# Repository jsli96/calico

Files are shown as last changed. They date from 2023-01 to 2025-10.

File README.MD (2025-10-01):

# Calico 🤖

Teaser

**Calico** is a miniature relocatable wearable system with fast and precise locomotion for on-body interaction, actuation and sensing. 
Calico consists of a two-wheel robot and an on-cloth track mechanism or "railway," on which the robot travels. 
The robot is self-contained, small in size, and has additional sensor expansion options. 
The Calico robot can adapt for various applications and target for different audience such as older adults, dancers, and children. 
For example, we designed **[Dance^2](https://dancesquared.xyz/)** with Calico to explore new forms of dance and movement, and to create a new form of interaction.
We also investigate how **[Calico for older adults](https://dl.acm.org/doi/10.5555/3721488.3721562)** can assist with daily activities and provide companionship. 

Please see the [Calico website](https://smartlab.cs.umd.edu/publication/calico) and [papers](https://dl.acm.org/doi/10.1145/3715336.3735828) for more details on the design and applications of Calico, and if you use Calico in your work, please consider to cite the following papers:
```
@article{sathya2022calico,
  title={Calico: Relocatable On-cloth Wearables with Fast, Reliable, and Precise Locomotion},
  author={Sathya, Anup and Li, Jiasheng and Rahman, Tauhidur and Gao, Ge and Peng, Huaishu},
  journal={Proceedings of the ACM on Interactive, Mobile, Wearable and Ubiquitous Technologies},
  volume={6},
  number={3},
  pages={1--32},
  year={2022},
  publisher={ACM New York, NY, USA}
}
```

```
@inproceedings{sathya2025cybernetic,
  title={Cybernetic Marionette: Channeling Collective Agency Through a Wearable Robot in a Live Dancer-Robot Duet},
  author={Sathya, Anup and Li, Jiasheng and Yan, Zeyu and Fang, Adriane and Kules, Bill and Martin, Jonathan David and Peng, Huaishu},
  booktitle={Proceedings of the 2025 ACM Designing Interactive Systems Conference},
  pages={3326--3340},
  year={2025}
}
```
```
@inproceedings{antony2025design,
  title={The design of on-body robots for older adults},
  author={Antony, Victor Nikhil and Jeon, Clara and Li, Jiasheng and Gao, Ge and Peng, Huaishu and Ostrowski, Anastasia K and Huang, Chien-Ming},
  booktitle={2025 20th ACM/IEEE International Conference on Human-Robot Interaction (HRI)},
  pages={589--598},
  year={2025},
  organization={IEEE}
}
```

---

## 📦 Table of Contents

- [Features](#-features)  
- [Hardware setup (BOM)](#-hardware)  
- [Arduino configuration](#arduino-configuration)
- [Connect & control the robot](#connect--control-the-robot)
- [Tips](#tips)

---

## ✨ Features

- MCU: ESP32 S3-Zero (Powered by [Waveshare](https://www.waveshare.com/wiki/ESP32-S3-Zero)) 
- Graphical user interface (GUI) for real time control
- Wi-Fi connection and controlled
- LED strip for visual feedback
- DC Motor Driver: DRV 8835
- LiPo's battery powered and charge via USB-C

---

## 🔧 Hardware

### Robot body and tracks 
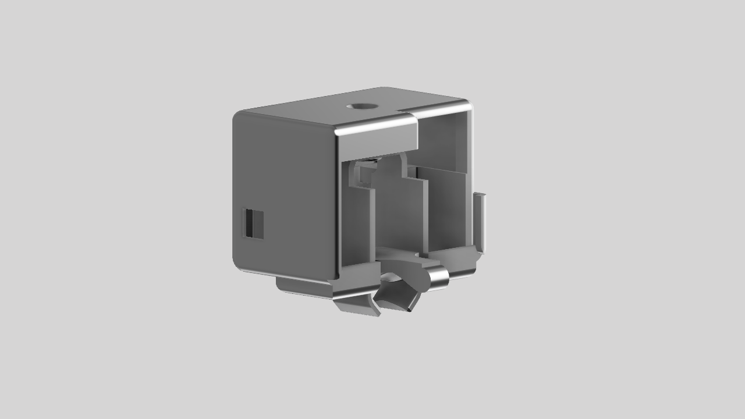
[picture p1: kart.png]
Robot body

- [Main body](./3D%20print%20models) 
  - 3D print material: PLA or Carbon PLA
  - Recommended print settings: 
    - Layer height: 0.2mm
    - Infill: 20% (or more for stronger body)
    - Print angle: 30 degrees
    - Supports: Yes 
  - Bamboo project file is included for reference: [3MF file](./3D%20print%20models/main_body.3mf)

- [Body cap](./3D%20print%20models) (Recommended setting same as above)
  - Require M2 screws and insert nuts to attach the body cap to the main body.
- [Wheels](./3D%20print%20models) (3D print material: PLA or Carbon PLA)
- [Track](./3D%20print%20models)
  - 3D print material: TPU Shore-95A
  - Recommended print settings: 
    - Layer height: 0.2mm
    - Infill: 20% 
    - Print angle: Flat (0 degrees)
    - Supports: Yes 
  - Bamboo project file is included for reference: [3MF file](./3D%20print%20models/track.3mf)
  - Tracks are designed in modular pieces, and you can print multiple pieces to create a longer track. 
    To connect the track pieces, you need a 1.75mm filament (e.g., PLA) and insert them into designed holes at the both end of the track pieces.
    
  - See below figures for references.
    Track assembly

### Robot electronics
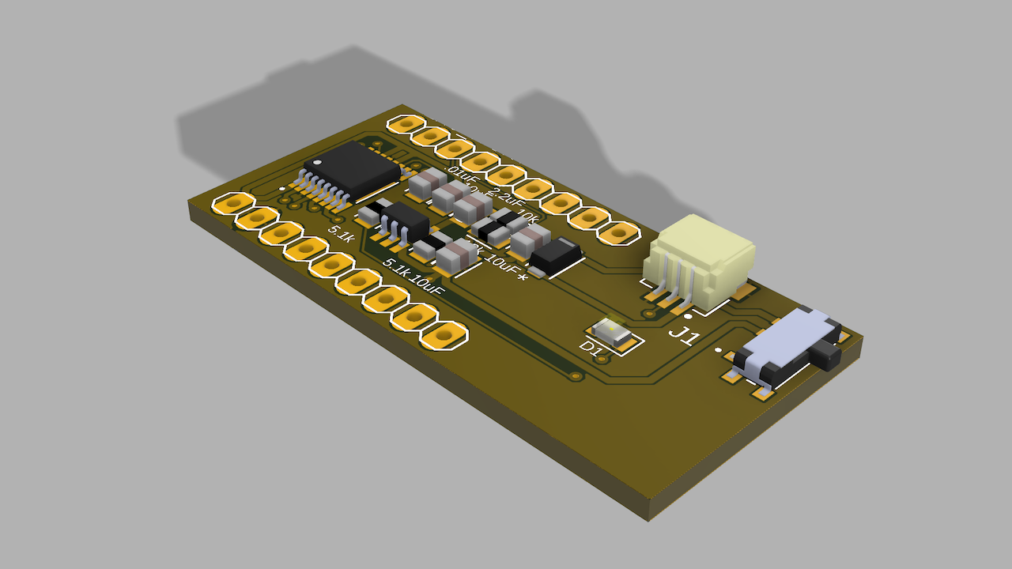
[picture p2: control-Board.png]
PCB

- MCU ([ESP32 S3-Zero](https://www.waveshare.com/wiki/ESP32-S3-Zero))
- Custom PCB ([See PCB folder for details](./PCB%20files))
- N20 DC motors
- LED strip (4 LEDs)
- 3.7V LiPo battery

---

## Arduino Configuration
The robot is powered by an ESP32 S3-Zero, which is programmed using the Arduino IDE. 
Please refer to the below steps to set up the Arduino IDE for Calico.
- Install the [Arduino IDE](https://www.arduino.cc/en/software).
- Open Arduino IDE settings (Mac Version) `Arduino IDE` (the top-left corner on the screen) > `Settings`, (Win version) `File` > `Preferences` 
- Adding the following URL to the "Additional Boards Manager URLs" field:
  ```
  https://dl.espressif.com/dl/package_esp32_index.json
  ```
- Open the Boards Manager from `Tools` > `Board` > `Boards Manager`, search for `esp32`. Then install the latest version of `esp32 by Espressif Systems`.
- Select the ESP32 S3-Zero board from `Tools` > `Board` > `ESP32 S3 Dev Module`.
- Refer to the below image to configure the ESP32 settings:
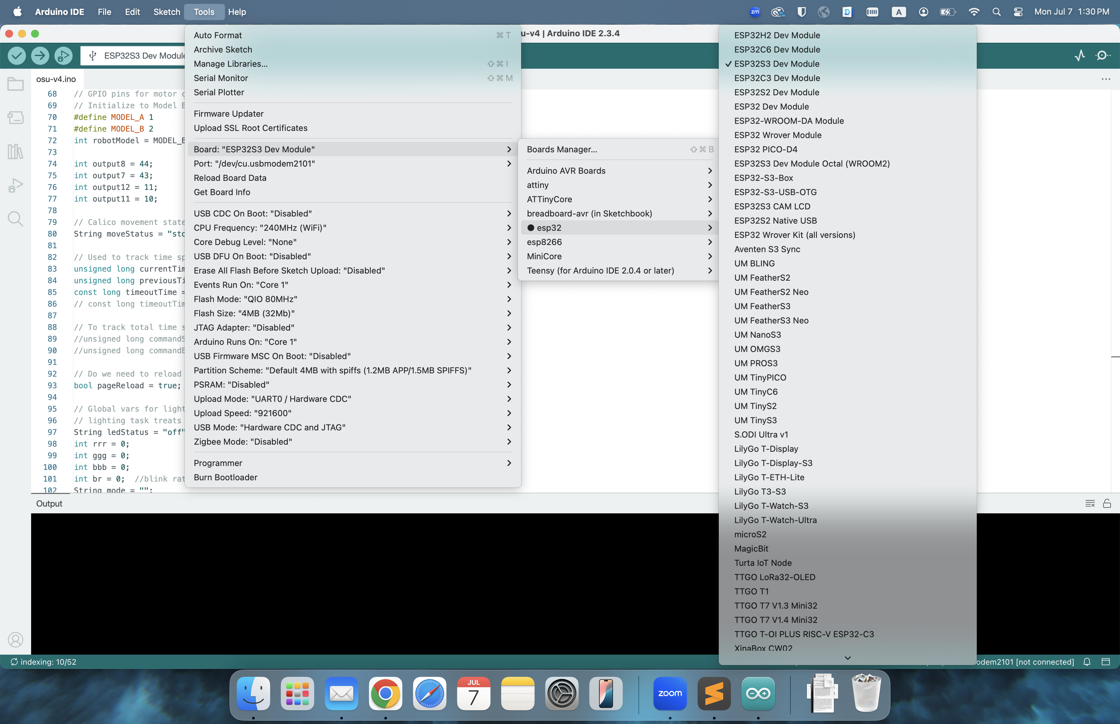
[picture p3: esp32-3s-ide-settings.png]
ESP32-S3
- 

---

## Connect & control the robot
To connect and control the robot, follow these steps:
1. **Connect the robot to your computer** using a USB-C cable.
2. **Open the Arduino IDE** and select the correct port from `Tools` > `Port`.
3. **Change the WiFi credentials** in the `main_app.ino' file (line 46 - 49) to match your network:
   ```
   const char* ssid_dev = "your-ssid";
   const char* password_dev = "your-password";
   const char* ssid = "your-ssid";
   const char* password = "your-password";
   ```
4. **Upload the code** to the ESP32 S3-Zero by clicking the upload button in the Arduino IDE. (You only need to do this once. 
After you have updated the Wi-Fi credentials and uploaded the code into Calico robot, you can control the robot without needing to upload the code again.)
   - Make sure you have the correct board and port selected in the Arduino IDE.
   - The upload process may take a few minutes, and you will see the progress in the console at the bottom of the IDE.
5. Once the upload is complete, open the Serial Monitor from `Tools` > `Serial Monitor` to see the connection status.
6. If the robot connects successfully, you will see a message indicating the IP address assigned to the robot.
7. **Open the GUI** by navigating to the IP address in your web browser. The GUI will allow you to control the robot's movement and LED strip.

## Tips
1. The robot will light up the LED light on board in different colors based on its status:
   - **light off**: Robot not powered
   - **steady blue**: Wi-Fi connected
   - **flashing blue**: Trying to connect Wi-Fi
   
2. If you can not see the ip address from the serial port you can use LanScan tools to find the IP address of the robot. 
   - For example, you can use [LanScan](https://apps.apple.com/us/app/lanscan/id472226235?mt=12) or [Advanced IP Scanner](https://www.advanced-ip-scanner.com/).

3. Battery connector is JST PH 2.0, and motor and LED connectors are JST SH 1.0.
4. The robot can be charged via USB-C port. (**be careful with the battery +/- directions**)
   - The battery is 3.7V LiPo battery, and the charging current is 500mA.
   - The battery can be replaced if needed.

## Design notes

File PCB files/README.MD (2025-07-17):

This is the PCB files folder for the Calico project. It contains the schematic and PCB design files for the custom control board used in the Calico robot.
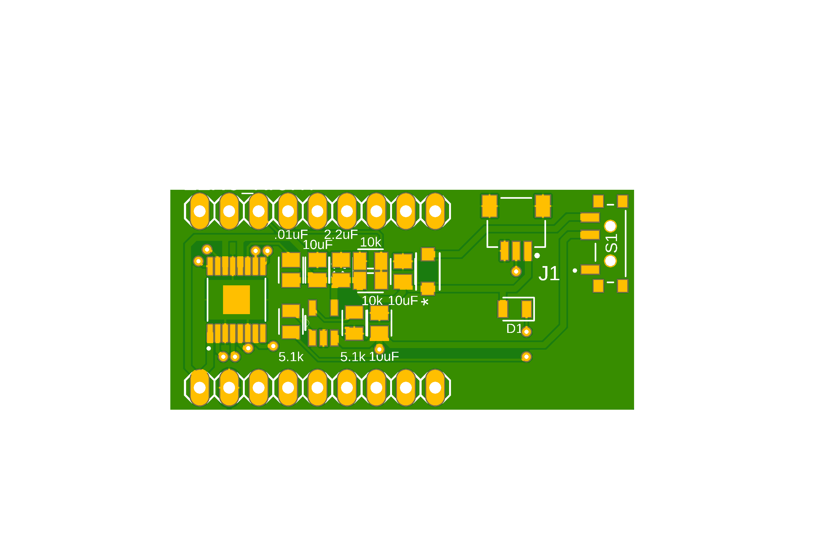
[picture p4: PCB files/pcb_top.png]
PCB-TOP

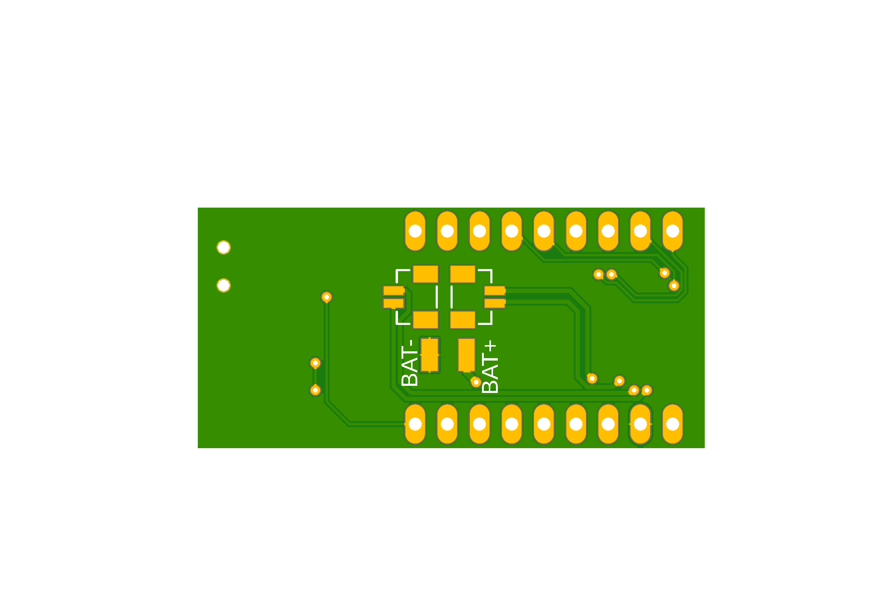
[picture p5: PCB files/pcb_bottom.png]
PCB-Bottom


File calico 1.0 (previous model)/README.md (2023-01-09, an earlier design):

# calico
Calico project

This project originally created and implemented by Anup (https://github.com/anupsathya/calico). 

This is a simplify version to help future development.

Change log:

Motor driver: DRV8833
```
  Motor 1: D25
           D22
  Motor 2: D19
           D17
```
RGB LED port: ```D5```

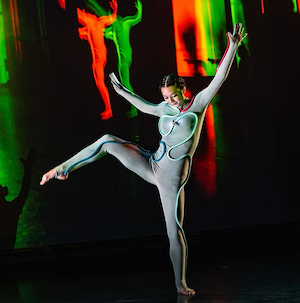
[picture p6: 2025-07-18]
calico_dancers.png

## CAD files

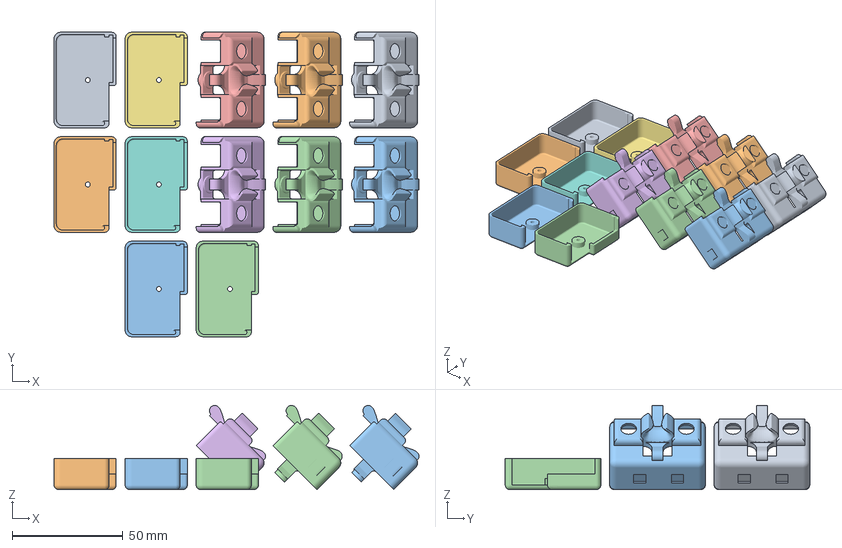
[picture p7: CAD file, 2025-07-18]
3D print models/main_body.3mf
164.5 x 137.3 x 37.9 mm
Main body.stl x 6
Body19.stl x 6

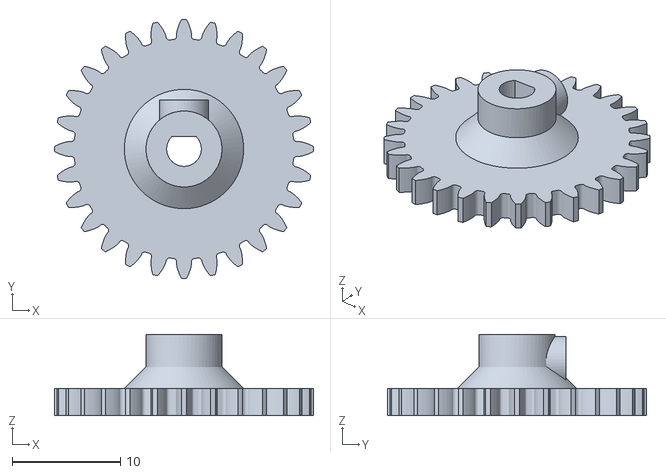
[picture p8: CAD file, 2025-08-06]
3D print models/wheel.stl
23.9 x 23.9 x 7.50

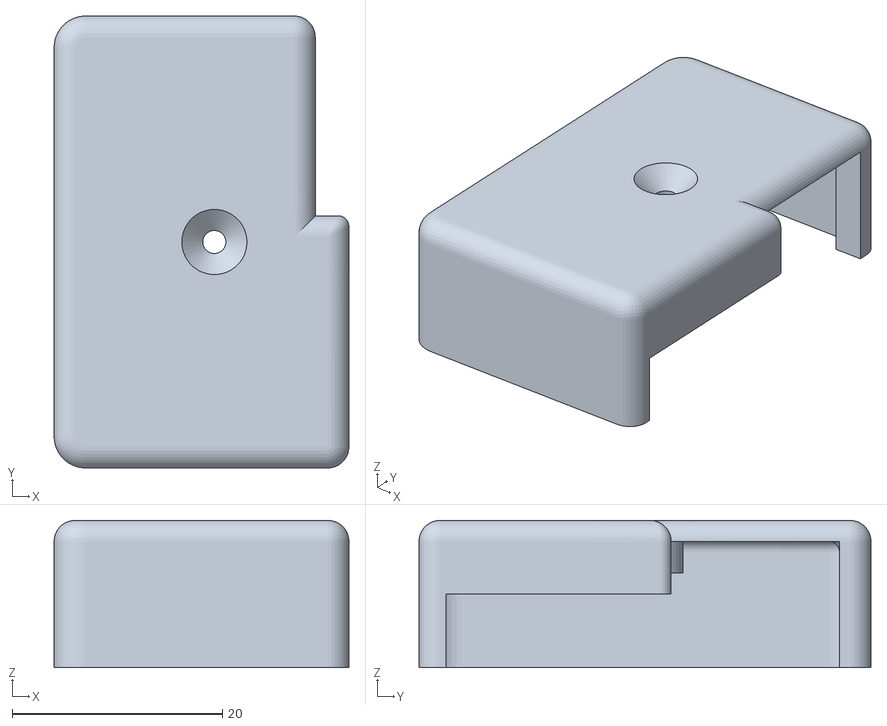
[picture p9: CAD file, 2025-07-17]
3D print models/cap.stl
28.1 x 43.0 x 14.0

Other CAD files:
3D print models/main_body.stl

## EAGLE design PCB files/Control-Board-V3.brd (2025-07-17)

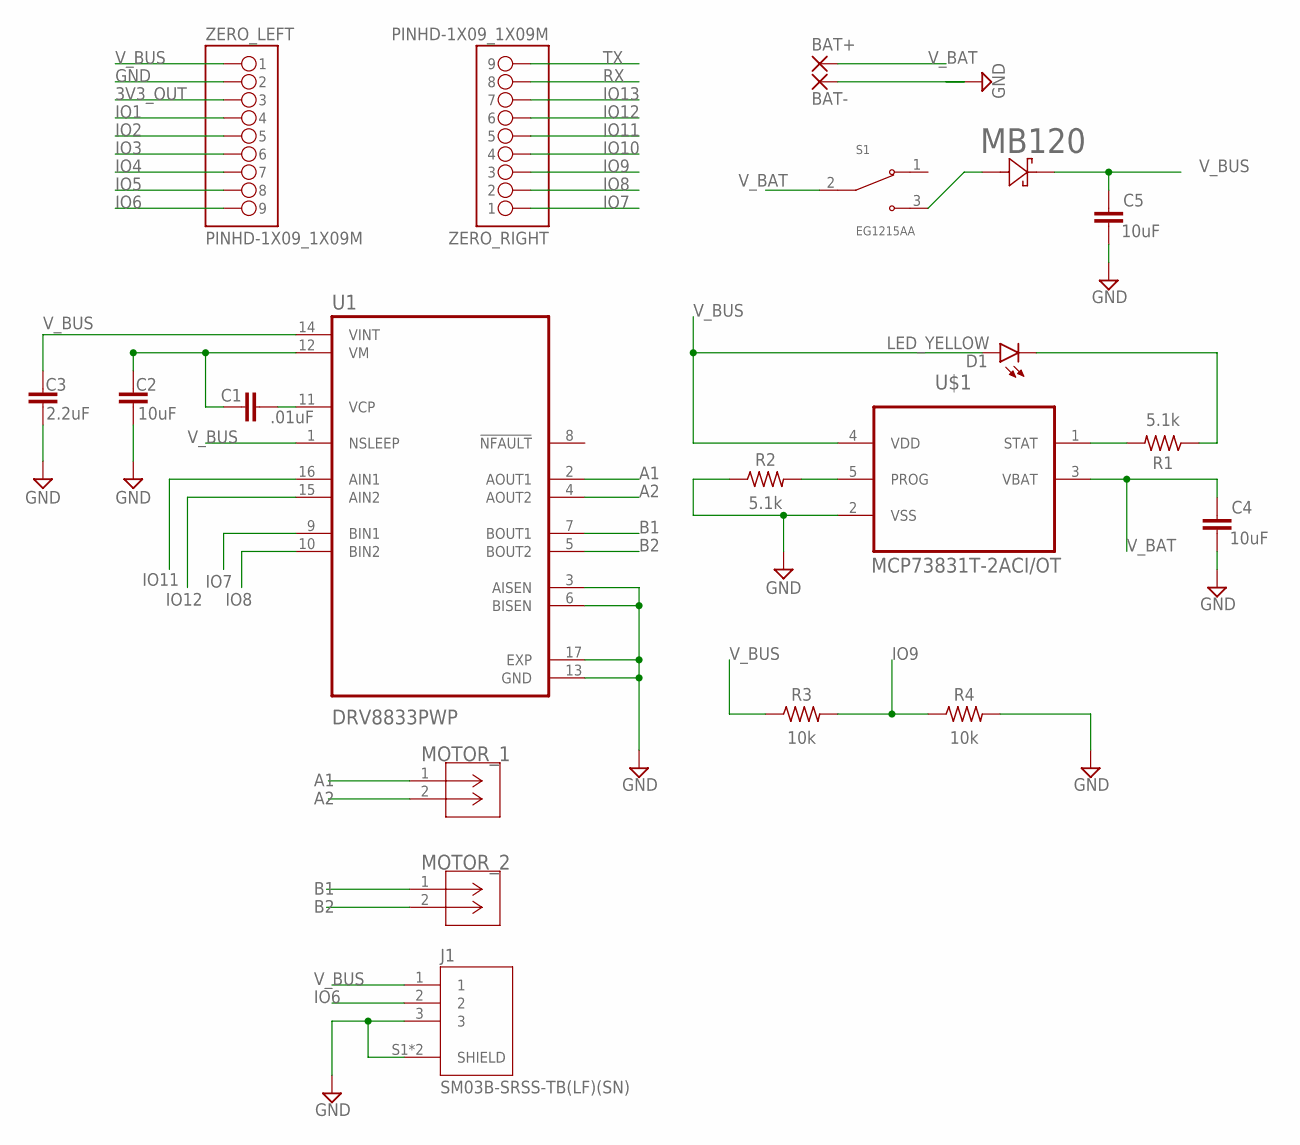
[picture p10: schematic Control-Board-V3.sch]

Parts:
BAT+: SMD2; SMD1,27-2,54
BAT-: SMD2; SMD1,27-2,54
C1: .01uF; CAPC2012X110
C2, C4, C5: 10uF; CAPC2012X110
C3: 2.2uF; CAPC2012X110
D1: LED_YELLOW; LEDC2012X110N_FLAT-Y
J1: SM03B-SRSS-TB(LF)(SN); JST_SM03B-SRSS-TB(LF)(SN)
MB120: MBR120LSFT3GSDO_SOD-123FL(498)_OSI-L; SDO_SOD-123FL(498)_OSI-L
MOTOR_1, MOTOR_2: JST_SH; JST
R1, R2: 5.1k; RESC2012X65
R3, R4: 10k; RESC2012X65
S1: EG1215AA; SW_EG1215AA
U1: DRV8833PWP; IC_DRV8833PWP
U$1: MCP73831T-2ACI/OT; SOT95P280X145-5N
ZERO_LEFT: PINHD-1X09_1X09M; 1X09
ZERO_RIGHT: PINHD-1X09_1X09M; 1X09

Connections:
3V3_OUT: ZERO_LEFT.3
A1: MOTOR_1.1, U1.2 (AOUT1)
A2: MOTOR_1.2, U1.4 (AOUT2)
B1: MOTOR_2.1, U1.7 (BOUT1)
B2: MOTOR_2.2, U1.5 (BOUT2)
GND: BAT-.1, C2.1, C3.1, C4.2, C5.2, J1.3, J1.S1 (SHIELD), J1.S2 (SHIELD), R2.1, R4.2, U1.3 (AISEN), U1.6 (BISEN), U1.13 (GND), U1.17 (EXP), U$1.2 (VSS), ZERO_LEFT.2
IO1: ZERO_LEFT.4
IO2: ZERO_LEFT.5
IO3: ZERO_LEFT.6
IO4: ZERO_LEFT.7
IO5: ZERO_LEFT.8
IO6: J1.2, ZERO_LEFT.9
IO7: U1.9 (BIN1), ZERO_RIGHT.1
IO8: U1.10 (BIN2), ZERO_RIGHT.2
IO9: R3.2, R4.1, ZERO_RIGHT.3
IO10: ZERO_RIGHT.4
IO11: U1.16 (AIN1), ZERO_RIGHT.5
IO12: U1.15 (AIN2), ZERO_RIGHT.6
IO13: ZERO_RIGHT.7
unnamed: C1.2, U1.11 (VCP)
unnamed: R1.2, U$1.1 (STAT)
unnamed: D1.C, R1.1
unnamed: R2.2, U$1.5 (PROG)
unnamed: MB120.2, S1.3
RX: ZERO_RIGHT.8
TX: ZERO_RIGHT.9
V_BAT: BAT+.1, C4.1, S1.2, U$1.3 (VBAT)
V_BUS: C1.1, C2.2, C3.2, C5.1, D1.A, J1.1, MB120.1, R3.1, U1.1 (NSLEEP), U1.12 (VM), U1.14 (VINT), U$1.4 (VDD), ZERO_LEFT.1

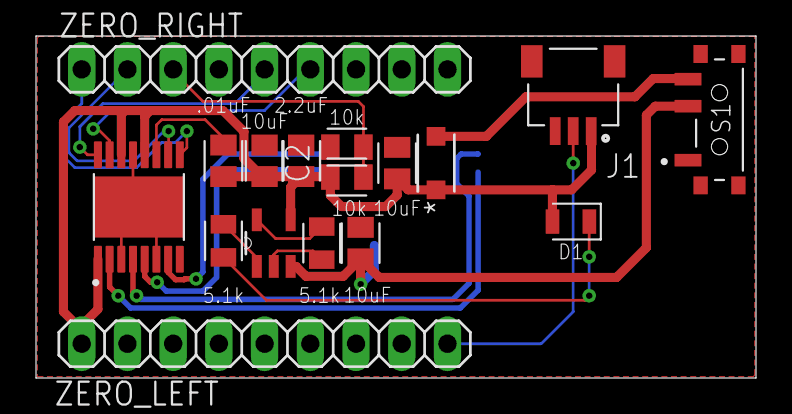
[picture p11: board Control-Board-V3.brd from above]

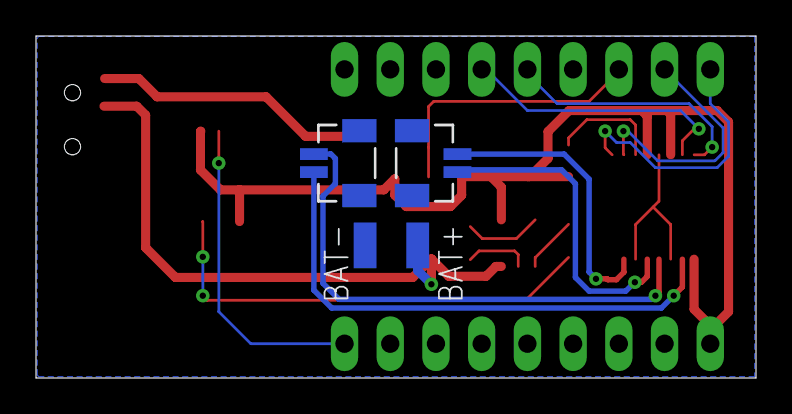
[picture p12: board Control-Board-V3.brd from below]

Board: 2 copper layers, 40.0 x 19.0 mm, 21 parts (4 on the bottom side), 18 nets.

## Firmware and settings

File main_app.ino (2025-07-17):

#include <WiFi.h>
#include <WiFiAP.h>
#include <WiFiClient.h>
#include <WiFiGeneric.h>
#include <WiFiMulti.h>
#include <WiFiSTA.h>
#include <WiFiScan.h>
#include <WiFiServer.h>
#include <WiFiType.h>
#include <WiFiUdp.h>

/*********
  Calico web control
  
  osc-v3 - 
  
  4/10 originally cloned from ..._ff_v02
  4/10 - change slow bink to go a bit quicker and fast blink to go a little slower
  4/12 - remove fade up/down; implement white light, multicolor and ALL OFF; reworked UI; tweaked slow blink duration 
  4/17 - added pulsate modes; bigger buttons; minor UI cleanups; removed unused mode colorsequence
  5/11 - add 2 vibrate modes
  5/13 - add nightlight mode
  12/12 - started OSU version - combined calico_sp24wk_1 with GPIO pin changes
  12/14 - streamlined serial printing; reduced timeoutTime to improve responsiveness
  12/20 - tweak code to show onboard & NeoPixel lights closer to the same time; pin lighting task to core 0; 
          streamline HTML printing
  1/7/2025 - Use XMLHttpRequest - Only reload page if empty request; otherwise just report result; trimmed HTML to 
          remove <a> and just leave <button>s. Anyone can send this request - QLab, Isadora, webdb server, etc. -
          as long as they have the right IP address.
  1/8/2025 - Add code to handle two robot models, which have different motor control pin assignments:
             Model A - original board, non-charging
             Model B - current board
  1/13/2025 - Keep LEDs dim after initial prod network connection AND when trying to connect to dev network

  To Do:
  - Set color w fade duration - keep current color
  
  Bugs:
  - if we get too many requests at once it drops things

  ********/

const char* calico_version = "mian_app";  // Make sure this matches file name

// Network credentials
const char* ssid_dev = "TP-LINK_lab0102";
const char* password_dev = "LAB0102!!!";
const char* ssid = "WIFI_0102";
const char* password = "admin0102";

#include <WiFi.h>
#include <Adafruit_NeoPixel.h>

// Pixel setup
#define LEDS_COUNT 4
#define LEDS_PIN 6
Adafruit_NeoPixel on_board_led(1, 21, NEO_RGB);
Adafruit_NeoPixel strip_led(LEDS_COUNT, LEDS_PIN, NEO_GRB);  // Note R/G are reversed compared to onboard LED

// Web server setup
WiFiServer server(80);
WiFiClient client;
String header;  // HTTP request
String ipAddr;

// Calico setup

// GPIO pins for motor control - we now support two robot models - see below
// Initialize to Model B - current
#define MODEL_A 1
#define MODEL_B 2
int robotModel = MODEL_B;

int output8 = 44;
int output7 = 43;
int output12 = 11;
int output11 = 10; 

// Calico movement state variable
String moveStatus = "stop";

// Used to track time spent reading client request - to make sure we don't hang indefinitely
unsigned long currentTime = millis();
unsigned long previousTime = 0;
const long timeoutTime = 200;  // Millisecs
// const long timeoutTime = 5000;  // Millisecs 

// To track total time spent processing each request
//unsigned long commandStart = 0;
//unsigned long commandEnd = 0;

// Do we need to reload entire page?
bool pageReload = true; // initially yes

// Global vars for lighting task
// lighting task treats these as read-only to avoid race conditions
String ledStatus = "off";
int rrr = 0;
int ggg = 0;
int bbb = 0;
int br = 0;  //blink rate in msecs (really this is the duration of half a cycle)
String mode = "";


// setColor - set color of onboard and LED strip
void setColor(uint32_t c) {
  on_board_led.setPixelColor(0, c);
  strip_led.fill(c);
  on_board_led.show();
  strip_led.show();
}

// In the future: Convert this to a fade up and down of blue... and call it from the lightign task... and create a button
// fadeColorOff - fade off over duration of time
// Use of vTaskDelay won't necessarily provide a consistent frequency - can use vTaskDelayUntil if needed
void fadeColorUp(int dur) {
  // char s[80];
  // sprintf(s, "fadeColorUp(): dur=%d\n", dur);
  // Serial.println (s);

  int iters = dur / 50;
  if (iters < 1) iters = 1;
  int inc_r = rrr / iters;
  int inc_g = ggg / iters;
  int inc_b = bbb / iters;
  int cur_r = 0;
  int cur_g = 0;
  int cur_b = 0;
  for (int i = 0; i < iters; i++) {
    cur_r += inc_r;
    cur_g += inc_g;
    cur_b += inc_b;
    setColor(Adafruit_NeoPixel::Color(cur_r, cur_g, cur_b));
    vTaskDelay(50 / portTICK_PERIOD_MS);  // converts msecs to ticks
  }
}

void fadeColorDown(int dur) {
  // char s[80];
  // sprintf(s, "fadeColorDown(): dur=%d\n", dur);
  // Serial.println (s);

  int iters = dur / 50;
  if (iters < 1) iters = 1;
  int inc_r = rrr / iters;
  int inc_g = ggg / iters;
  int inc_b = bbb / iters;
  int cur_r = rrr;
  int cur_g = ggg;
  int cur_b = bbb;
  for (int i = 0; i < iters; i++) {
    cur_r -= inc_r;
    cur_g -= inc_g;
    cur_b -= inc_b;
    setColor(Adafruit_NeoPixel::Color(cur_r, cur_g, cur_b));
    vTaskDelay(50 / portTICK_PERIOD_MS);  // converts msecs to ticks
  }
}

// Lighting task setup
// Uses global var ledStatus as state variable
void lightingTask(void* parameters) {
  int count = 0;
  Serial.print("Lighting task running on core ");
  Serial.println(xPortGetCoreID());
  for (;;) {
    //  Serial.println("lightingTask(): ledStatus=" + ledStatus);

    if (ledStatus == "Off") {
      on_board_led.clear();
      strip_led.clear();
      on_board_led.show();
      strip_led.show();
    } else if (ledStatus == "light") {
      //  char s[80];
      //  sprintf(s, "RGB: %d, %d, %d, br: %d\n", rrr, ggg, bbb, br);
      //  Serial.println (s);

      if (br <= 0 || br > 4000) {  // non-blinking - note max blink duration is 4 sec
        setColor(Adafruit_NeoPixel::Color(rrr, ggg, bbb));
      } else {  // blinking
        setColor(Adafruit_NeoPixel::Color(rrr, ggg, bbb));
        vTaskDelay(br / portTICK_PERIOD_MS);  // converts msecs to ticks
        on_board_led.clear();
        strip_led.clear();
        on_board_led.show();
        strip_led.show();
        vTaskDelay(br / portTICK_PERIOD_MS);  // converts msecs to ticks
      }

    } else if (ledStatus == "multicolor") {
      setColor(Adafruit_NeoPixel::Color(255, 0, 0));
      delay(200);
      setColor(Adafruit_NeoPixel::Color(0, 255, 0));
      delay(200);
      setColor(Adafruit_NeoPixel::Color(0, 0, 255));
      delay(100);  // only 100 here b/c the task delays 100 below

    } else if (ledStatus == "pulsate") {
      fadeColorUp(br);
      fadeColorDown(br);
    }
    //  Adjust task stack size to match high water mark eventually
    //    int stackSize = uxTaskGetStackHighWaterMark(NULL);
    //    Serial.println(stackSize);
    vTaskDelay(100 / portTICK_PERIOD_MS);  // converts msecs to ticks
  }
}

void moveStop() {
  Serial.println("Motor Stop");
  moveStatus = "stop";
  digitalWrite(output8, HIGH);
  digitalWrite(output7, HIGH);
  digitalWrite(output12, HIGH);
  digitalWrite(output11, HIGH);
}

void moveForward() {
  moveStatus = "Forward";
  digitalWrite(output8, LOW);
  digitalWrite(output7, HIGH);
  digitalWrite(output12, LOW);
  digitalWrite(output11, HIGH);
}

void moveBackward() {
  moveStatus = "Backward";
  digitalWrite(output8, HIGH);
  digitalWrite(output7, LOW);
  digitalWrite(output12, HIGH);
  digitalWrite(output11, LOW);
}

void setRobotModel(int model) {
  robotModel = model;
  if (model == MODEL_B) {
    // Model B - current
    output8 = 44;
    output7 = 43;
    output12 = 11;
    output11 = 10;
  } else if (model == MODEL_A) {
    output8 = 8;
    output7 = 7;
    output12 = 12;
    output11 = 11;
  }

  // Configure motor control pins?
  pinMode(output8, OUTPUT);
  pinMode(output7, OUTPUT);
  pinMode(output12, OUTPUT);
  pinMode(output11, OUTPUT);

  // Set outputs to LOW - Why? This is differnet than stop (below)
  digitalWrite(output8, LOW);
  digitalWrite(output7, LOW);
  digitalWrite(output12, LOW);
  digitalWrite(output11, LOW);
}

void setup() {
  Serial.begin(115200);
  while (!Serial)
    ;  // Delay until Serial port is available?
  Serial.print("Calico is here: ");
  Serial.println(calico_version);

  Serial.print("Setup task running on core ");
  Serial.println(xPortGetCoreID());

  // LED setup
  on_board_led.begin();
  on_board_led.clear();
  on_board_led.setPixelColor(0, 0xFF0000);
  on_board_led.show();

  // Set up motor control -- current model is B
  setRobotModel(MODEL_B);

  // Connect to Wi-Fi show network with SSID and password
  Serial.print("Connecting to show network:");
  Serial.println(ssid);
  WiFi.begin(ssid, password);
  int tries = 0;
  setColor(0x020000);
  while (WiFi.status() != WL_CONNECTED && tries < 6) {
    //setColor(0x000000);
    delay(500);
    //setColor(0xFF0000);
    tries++;
    Serial.print(".");
  }

  // Dev network
  if (WiFi.status() != WL_CONNECTED) {
    setColor(0x000200);
    WiFi.disconnect();
    Serial.print("\nConnecting to dev network: ");
    Serial.println(ssid_dev);
    WiFi.begin(ssid_dev, password_dev);
    while (WiFi.status() != WL_CONNECTED) {
      //setColor(0x000000);
      delay(500);
      //setColor(0x00FF00);
      Serial.print(".");
    }
  }

  // Print local IP address and start web server
  Serial.println("");
  Serial.print("WiFi connected. IP address: ");
  Serial.println(WiFi.localIP());
  ipAddr = WiFi.localIP().toString();

  server.begin();
  Serial.println("called server.begin()");
  on_board_led.setPixelColor(0, 0x00FF00);
  on_board_led.show();
  strip_led.begin();
  strip_led.clear();

  // Light task initiation
  delay(1000);  // Give time for wifi connection? Or maybe directly test as above...
  /*
  xTaskCreate(
    lightingTask,    // task function name
    "lightingTask",  // description
    100000,          // stack size in bytes - make it big for now (currently using about 33kB)
    NULL,            // parameters - not used
    0,               // priority - low priority compared to main task
    NULL             // task handle - not used
  );
  Serial.println("Created lightingTask()");
  */

  xTaskCreatePinnedToCore(
    lightingTask,    // task function name
    "lightingTask",  // description
    100000,          // stack size in bytes - make it big for now (currently using about 33kB)
    NULL,            // parameters - not used
    0,               // priority - low priority compared to main task
    NULL,            // task handle - not used
    0                // pin task to core 0
  );
  delay(500);
  Serial.println("Created lightingTask()");

  ledStatus = "light";
  rrr = 0;
  ggg = 0;
  bbb = 255;
}

void loop() {
//  Serial.println("Server ready");
//  Serial.println("");
  // Serial.print("Main loop running on core ");
  // Serial.println(xPortGetCoreID());

//  if (pageReload == true) {
//    Serial.println("pagereload is true: get a client");
    client = server.available();  // Listen for incoming clients
//  } else {
//        Serial.println("pagereload is false: assume we already have a client");
//  }

  if (client) {  // If a new client connects,
    currentTime = millis();
    previousTime = currentTime;
    Serial.print("Request: ");  // print a message out in the serial port
    String currentLine = "";        // make a String to hold incoming data from the client

//    Serial.println(client.connected());

    while (client.connected() && currentTime - previousTime <= timeoutTime) {  // loop while the client's connected, as long as we havent timed out
      // Serial.println ("Client connected");
      currentTime = millis();
      if (client.available()) {  // if there's bytes to read from the client,
        char c = client.read();  // read a byte, then
        // Serial.print(c);         // print it out the serial monitor
        header += c;

        if (c == '\n') {  // There should be one line for the GET request, plus a blank line;
                          // if we are at the end of the line we might have a request to process

          // if the current line is blank, we got two newline characters in a row.
          // that's the end of the client HTTP request, so process the request and send a response:
          //Serial.print("\nFound newline; processing header:");
          //Serial.println(header);
          if (currentLine.length() == 0) {
            //Serial.print("\ncurrentLine is empty");

            // Only reload page if needed
            pageReload = false;

            //commandStart = millis();

            // turns the GPIOs on and off - controls the motors
            if (header.indexOf("GET /move/stop") >= 0) {
              Serial.println("Stop");
              moveStatus = "stop";
              digitalWrite(output8, HIGH);
              digitalWrite(output7, HIGH);
              digitalWrite(output12, HIGH);
              digitalWrite(output11, HIGH);
            } else if (header.indexOf("GET /move/forward") >= 0) {
              Serial.println("Forward");
              moveStatus = "Forward";
              digitalWrite(output8, LOW);
              digitalWrite(output7, HIGH);
              digitalWrite(output12, LOW);
              digitalWrite(output11, HIGH);
            } else if (header.indexOf("GET /move/backward") >= 0) {
              Serial.println("Backward");
              moveStatus = "Backward";
              digitalWrite(output8, HIGH);
              digitalWrite(output7, LOW);
              digitalWrite(output12, HIGH);
              digitalWrite(output11, LOW);
            }
            else if (header.lastIndexOf("GET /v1") >= 0) {
              // Need to move this into a separate task to avoid blocking the web server
              Serial.println("Vibe 1");
              moveStatus = "V1";

              for (int i = 0; i < 5; i++) {
                moveForward();
                delay(100);
                moveBackward();
                delay(100);
              }
              moveStop();
            } else if (header.lastIndexOf("GET /v2") >= 0) {
              Serial.println("Vibe 2");
              moveStatus = "V2";

              for (int i = 0; i < 10; i++) {
                moveForward();
                delay(200);
                moveBackward();
                delay(200);
              }
              moveStop();
            }

            // Set up robot model
            else if (header.indexOf("GET /setRobotModelA") >= 0) {
              setRobotModel(MODEL_A);
              pageReload = true;
            }

            else if (header.indexOf("GET /setRobotModelB") >= 0) {
              setRobotModel(MODEL_B);
              pageReload = true;
            }

            // Stop and turn off lights
            else if (header.indexOf("GET /alloff") >= 0) {
              Serial.println("ALL OFF");
              ledStatus = "Off";
              moveStatus = "stop";
              digitalWrite(output8, HIGH);
              digitalWrite(output7, HIGH);
              digitalWrite(output12, HIGH);
              digitalWrite(output11, HIGH);
              pageReload = true;
            }

            // Lighting control
            else if (header.indexOf("GET /led/multicolor") >= 0) {
              Serial.println("Multicolor");
              ledStatus = "multicolor";
            } else if (header.indexOf("GET /led/pulseslow") >= 0) {
              Serial.println("Pulse slow");
              ledStatus = "pulsate";
              br = 1200;
            } else if (header.indexOf("GET /led/pulsemedium") >= 0) {
              Serial.println("Pulse med");
              ledStatus = "pulsate";
              br = 600;
            } else if (header.indexOf("GET /led/pulsefast") >= 0) {
              Serial.println("Pulse fast");
              ledStatus = "pulsate";
              br = 200;
            } else if (header.indexOf("GET /led/blinkslow") >= 0) {
              Serial.println("Blink slow");
              ledStatus = "light";
              br = 1200;  // 4/10 - changed 2000 to 1500 to speed it up a bit; 4/12 - changed to 1200
            } else if (header.indexOf("GET /led/blinkmedium") >= 0) {
              Serial.println("Blink med");
              ledStatus = "light";
              br = 600;
            } else if (header.indexOf("GET /led/blinkfast") >= 0) {
              Serial.println("Blink fast");
              ledStatus = "light";
              br = 200;  // change 100 to 200 to slow it down a bit (avoid trigger frequency)
            } else if (header.indexOf("GET /led/solid") >= 0) {
              Serial.println("Solid");
              ledStatus = "light";
              br = 0;
            } else if (header.indexOf("GET /led/red") >= 0) {
              Serial.println("Red");
              ledStatus = "light";
              br = 0;
              rrr = 255;
              ggg = 0;
              bbb = 0;
            } else if (header.indexOf("GET /led/green") >= 0) {
              Serial.println("Green");
              ledStatus = "light";
              br = 0;
              rrr = 0;
              ggg = 255;
              bbb = 0;
            } else if (header.indexOf("GET /led/blue") >= 0) {
              Serial.println("Blue");
              ledStatus = "light";
              br = 0;
              rrr = 0;
              ggg = 0;
              bbb = 255;
            } else if (header.indexOf("GET /led/white") >= 0) {
              Serial.println("White");
              ledStatus = "light";
              br = 0;
              rrr = 255;
              ggg = 255;
              bbb = 0xF0;  // make it a little less blue
            } else if (header.indexOf("GET /led/nightlight") >= 0) {
              Serial.println("Night light");
              ledStatus = "light";
              br = 0;
              rrr = 25;
              ggg = 25;
              bbb = 20;  // make it a little less blue
            } else if (header.indexOf("GET /led/off") >= 0) {
              Serial.println("Light off");
              ledStatus = "Off";
            } else {
              pageReload = true;
            }

            //commandEnd = millis();

            if (pageReload == false) {
              // HTTP headers always start with a response code (e.g. HTTP/1.1 200 OK)
              // and a content-type so the client knows what's coming, then a blank line:
              client.println("HTTP/1.1 200 OK \n \
              Content-type:text/html \n \
              Connection: Keep-Alive");
              // The HTTP response ends with another blank line
              client.println();

            } else {

              // HTTP headers always start with a response code (e.g. HTTP/1.1 200 OK)
              // and a content-type so the client knows what's coming, then a blank line:
              //client.println("HTTP/1.1 200 OK \n \
              Content-type:text/html \n \
              Connection: close");
              // Keep connection open
              client.println("HTTP/1.1 200 OK                            \n \
Content-type:text/html \n");
              client.println();
              // Display the HTML web page
              client.println("<!DOCTYPE html><html> \n \
              <head><meta name=\"viewport\" content=\"width=device-width, initial-scale=1\"> \n \
              <title>Calico Control</title> \n \
              <link rel=\"icon\" href=\"data:,\">");
              // CSS to style the buttons
              // Feel free to change the background-color and font-size attributes to fit your preferences (was #4CAF50;)
              client.println("<style>html { font-family: Helvetica; display: inline-block; margin: 0px auto; text-align: center;} \n \
              .button { background-color: #999999; border: none; color: white; padding: 28px 40px; border-radius: 14px; \n \
              text-decoration: none; font-size: 28px; margin: 2px; cursor: pointer;} \n \
              .buttonRed { background-color: #FF0000 } \n \
              .buttonGreen { background-color: #00FF00 } \n \
              .buttonBlue { background-color: #000099; } \n \
              .buttonGray { background-color: #999999; } \n \
              .buttonBlack { background-color: #000000; } \n \
              .buttonPurple { background-color: #A56ED8; } \n \
              .buttonLightblue { background-color: lightblue; } \n \
              .buttonWhite { background-color: white; border-style: solid; border-color: black; color: black; padding: 30px 40px; \n \
              text-decoration: none; font-size: 26px; margin: 2px; cursor: pointer;} \n \
              </style></head>");

              // Combined multiple prints to streamline printing; saved a few millis but probably not a lot

              // Web Page Heading
              client.println("<body onload=pageload()>");
              // char s[200];
              // sprintf(s, "<h2>Movement: %s &nbsp;&nbsp;&nbsp;&nbsp;&nbsp;&nbsp;&nbsp;&nbsp;&nbsp;&nbsp; Lights: %s [%d, %d, %d], br: %d</h2>\n", moveStatus, ledStatus, rrr, ggg, bbb, br);
              // client.println(s);

              // JS to send HTTP requests
              client.print("<script> \n \
                const ipAddr = \'");
              client.print(ipAddr);
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

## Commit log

2023-01-09 update new files
    web buttons updated
2023-03-04 added white led
2023-03-04 reordered the buttons
2023-03-04 decrease the led auto changing time interval.
2023-03-04 decrease the white led power to 55/255
2023-03-08 add fast led auto changing
2025-07-17 update calico 2.0 files
    [Control-Board-V3-Charging v54.brd, Control-Board-V3-Charging_v21.sch, cap.stl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]
2025-07-17 update calico README.MD
    [Control-Board-V3.brd, Control-Board-V3.sch]

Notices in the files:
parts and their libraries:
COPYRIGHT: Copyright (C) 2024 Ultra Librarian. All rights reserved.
